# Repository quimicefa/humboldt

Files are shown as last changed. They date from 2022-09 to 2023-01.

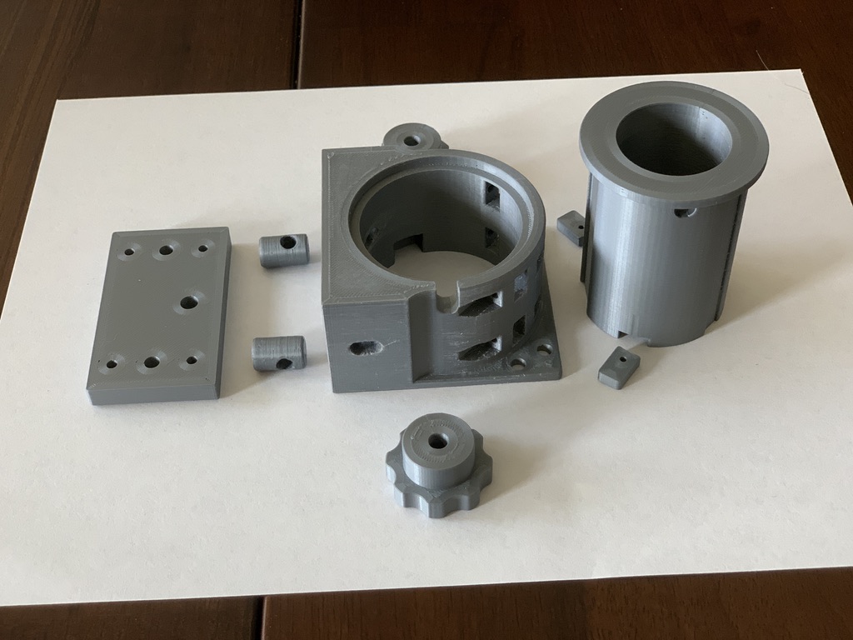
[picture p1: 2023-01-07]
focuser/images/focuser_125_ex_3D_PLA_parts.jpeg

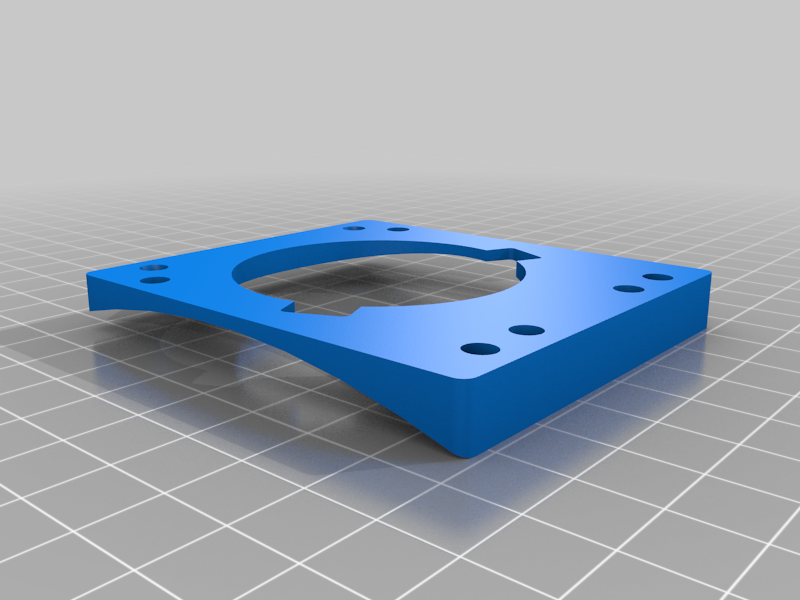
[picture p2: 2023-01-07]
focuser/images/focuser_1-25_curved_base_10-25_dia.png

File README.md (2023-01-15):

# Humboldt telescope
<p>Mashup from Leavitt LITE (Metric)</p>

<p>OTA by Aurelian on Printables: https://www.printables.com/es/model/355997-8-newtonian-telescope-leavitt-lite-metric</p>
<p>Crayford Focuser 1 1/4 inch by scbeme on Thingiverse: https://www.thingiverse.com/thing:5167331</p>

***

Focuser:

| id | Part | Dimensions | Material | Qty | Ref  | notes |
| -- | --- | --- | --- | ----- | ---- | --- |
| 1  | Drawtube | [Ref Drawing](focuser/files/focuser-drawtube_ver2.stl) | PLA | 1 | | |
| 2  | Base | [Ref Drawing](focuser/files/focuser_1-25_base.stl) | PLA | 1 | | |
| 3  | Curved base | [Ref Drawing](focuser/files/focuser_1-25_curved_base_10-25_dia.stl) | PLA | 1 | | Fits 10.25” OD tube |
| 4  | Pinion pressure rod | [Ref Drawing](focuser/files/focuser-pressure_cylinder_ver2.stl) | PLA | 2 | | |
| 5  | Base back | [Ref Drawing](focuser/files/focuser_1-25_back.stl) | PLA | 1 | | |
| 6  | Knob | [Ref Drawing](focuser/files/focuser-knob_ver2.stl) | PLA | 2 | | |
| 7  | Drawtube stop | [Ref Drawing](focuser/files/focuser_1-25_drawtube_stop_M2.stl) | PLA | 2 | | |
| 8  | Drawtube bearing rail | 2mm x 6mm x 60mm | Aluminium / Brass | 2 |  [LM-2](https://www.leroymerlin.es/productos/ferreteria-y-seguridad/perfiles-pletinas-chapas-y-rejillas/perfiles/plano-de-aluminio-gris-alt-0-2-x-an-1-5-x-l-100-cm-80109393.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) | |
| 9  | Drawtube pinion rail | 2mm x 12.5mm x 60mm | Aluminium | 1 |  [LM-2](https://www.leroymerlin.es/productos/ferreteria-y-seguridad/perfiles-pletinas-chapas-y-rejillas/perfiles/plano-de-aluminio-gris-alt-0-2-x-an-1-5-x-l-100-cm-80109393.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) | |
| 10 | M4 Philips head screw | 4mm x 20mm | Nylon | 1 | | Drawtube eyepiece capture screw |
| 11 | M3 button head hex drive screw | 3mm x 12mm | Stainless | 4+4 | | Base back / Curved base mounting screws |
| 12 | Pinion rod | d=4mm L=96mm | Stainless | 1 | [LM-1](https://www.leroymerlin.es/productos/ferreteria-y-seguridad/perfiles-pletinas-chapas-y-rejillas/perfiles/perfil-forma-redonda-de-acero-4mm-x-l-100-cm-80110632.html) | |
| 13 | Bearings | 8mm OD x 3mm ID x 4mm (693ZZ) | Stainless | 4 | [AE-2](https://www.aliexpress.com/item/4000980546028.html?spm=a2g0o.order_list.order_list_main.11.6c1218026v9wbl) | |
| 14 | M3 cap head hex screw | 3mm x 20mm | Stainless | 4 | | Bearing shafts |
| 15 | M3 flat washers | 3mm | Stainless | 8 | | Bearing shaft washers |
| 16 | M3 hex nuts | 3mm | Stainless | 4 | | Bearing shaft nuts |
| 17 | M3 heat set inserts | 3mm x 6mm L | Brass | 4+2+4 | [AE-1](https://www.aliexpress.com/item/1005003174906572.html?spm=a2g0o.order_list.order_list_main.5.21ef194dLnVGNK) | Base back / Knobs / Curved base |
| 18 | M4 heat set inserts | 4mm x 6mm L | Brass | 2 | [AE-1](https://www.aliexpress.com/item/1005003174906572.html?spm=a2g0o.order_list.order_list_main.5.21ef194dLnVGNK) | Eyepiece capture screw insert / Optional brake screw insert |
| 19 | M3 grub screws | 3mm x 6mm L | Stainless | 2+2+4 | | Knobs / Pinion pressure screws / Curved base alignment |
| 20 | M2 button head hex drive screw | 2mm x 8mm | Stainless | 2 | | Drawtube stops |
| 21 | M2 heat set inserts | 2mm x 6mm | Brass | 2 | [AE-1](https://www.aliexpress.com/item/1005003174906572.html?spm=a2g0o.order_list.order_list_main.5.21ef194dLnVGNK) | Drawtube stop inserts |

***
https://www.bauhaus.es/perfiles-metalicos-y-de-pvc/alberts-barra-plana/p/22847159
*** 

bearing rails (x2):
	w:6mm 
	l: 60mm
	t: 1mm
	
pinion rail (x1):
	w: 12.5mm
	l: 60mm
	t: 1.5mm

https://es.aliexpress.com/item/557757520.html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	
bearings (x4) 693ZZ:
	OD: 8mm
	ID: 3mm
	w: 4mm

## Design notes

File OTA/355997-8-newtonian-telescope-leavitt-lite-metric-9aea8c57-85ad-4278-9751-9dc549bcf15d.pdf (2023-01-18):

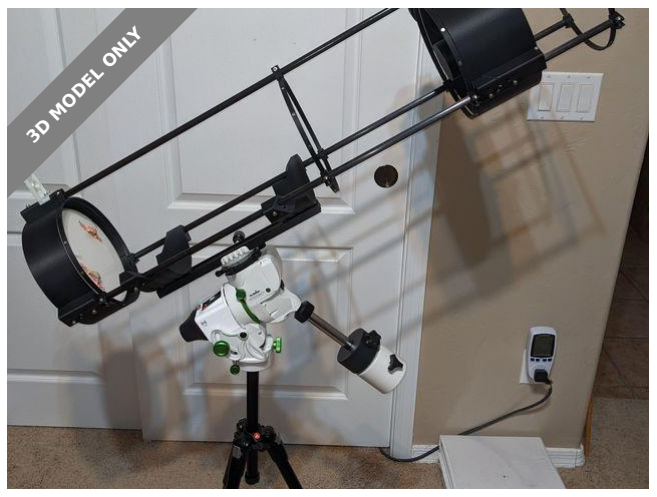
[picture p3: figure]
3D MODEL ONLY

## Summary

Based on Novel Tinker's 8" Leavitt keeping roughly the same design, but with the aim to be extremely lightweight (~8lbs)

Learning (https://printables.com/model?categoryId=90) > Physics & Astronomy (https://printables.com/model?categoryId=91)

Tags: astronomy | astrophotography | newtonian
newtoniantelescope | planets | reflector | science | stars

telescope

The Leavitt LITE takes the original Leavitt by Novel Tinker and does a few different notable things :

Use metric M4 screws & 12mm rods, this falls inline with a transition from the Hadley to Leavitt if you're coming from the official Hadley Metric Remix (https://www.printables.com/model/268580-hadley-telescope-remix-metric-mods-more)
Uses a 62.5mm secondary mirror (recommended (https://agenaastro.com/gso-parabolic-primary-telescope-mirror-8-f-5-ad049.html) for best uniform illumination on an F5 200mm mirror, can also cross reference with secondary mirror calculator (http://www.bbastrodesigns.com/NewtDesigner.html#diagonal)
Uses an overall smaller outer radius on parts (109mm) and thinner (but still sturdy) walls & rod interfaces to cut down on weight. It isn't much but it adds up!

Aurelian (https://printables.com/social/513907/about)

## 8" Newtonian Telescope "Leavitt"

## LITE (Metric)

VIEW IN BROWSER (https://printables.com/model/355997-8-newtonian-telescope-leavitt-lite-metric)

updated 17. 1. 2023 | published 17. 1. 2023

•

•

•

No conversion for Dobsonian mount, instead a mount interface for a Vixen Dovetail is provided with M5 screw holes
Slight modifications to spider + sights to fit new layout
Focuser clamp knob in case you don't want to buy thumb screws Primary cell changed to 120mm radius inner circle, 6 raised points of contact with small holes for better adhesion
Inner circle widening meant to both distribute the weight more and allow heatsinks to be attached to the back. My plan is to attach four 40mmx40mm heatsinks and have a quick-attach 120mm fan actively cool (WIP)

All that said, much of the credit and design goes to Novel Tinker for coming up with something that would fit on most print beds. Additionally, the basics of assembly instructions remains the same (using metric screws though) with some minor edits for QoL improvements:

Use two (2) triangular turn knobs for the secondary cell main height screw and on the primary cell adjustment screws (one on either side of the LTA so once collimated you can easily turn them to lock) for a total of eight (8) knobs (see close up photos)
You can use a spring as well on the primary cell adjustment screws, but the mirror is soooo heavy I wouldn't count on it Use a nut on underside of primary cell and on top of spider for secondary cell adjustments to lock screw (see close up photos)
Do the spider/secondary cell nut to lock the screw after collimation!
Can and probably should use a nut on the secondary cell main screw to lock in place
Put glue all along the top flat outer ring of the primary cell and then once mirror is placed along the rim on the underside, using finger or popsicle stick to smooth out. Last thing you want is your very expensive primary mirror falling out (see dead-on photo of back of primary mirror - all the silvery stuff is the glue)

Files that remain the same and should be sourced from the original Leavitt (https://www.printables.com/model/299531-8-newtonian-telescope-leavitt/files) :

Focuser grub
Focuser inner
Focuser ring
1.25 inch eyepiece adapter

##EDITS##

Added the blender file in which this was made. Unless you're computer is fast you may face some “issues” with it running slow, such is the nature of many many modifiers.

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
Added ribbed braced alternatives for the UTA, LTA could be done but is already fairly sturdy
Added a thicker spider alternative. Does cut down on light capture but is far sturdier
Added a little more tolerance to the secondary cell holder. Rising walls may be frail but that is okay, you should glue from the back anyways to avoid stressing the mirror during thermal acclimation

Overall using a mixture of the original Leavitt instructions and the above edits, the telescope is rock solid. In order to cut down on weight further I used 12mm 1000mm length carbon fiber rods. Pre-mirror installation the whole OTA including the ~300g long aluminum dovetail I have on it weighed 1660g (3.66lbs). With mirrors installed the OTA comes out to about 3855g (~8.5lbs)! This is light enough that I'm running it on a Star Adventurer GTI with accurate GoTo and tracking with a phone or camera attached (pictures of captures using these setups attached).

The whole purpose was to prove that you could do DSO astrophotography with maximal aperture (aperture is king alongside exposure - don't listen to those who say aperture isn't important) on a system that costs ~$1k USD. Likewise to prove that you can mount a large Newtonian on something less than an EQR-6. I will continue to post pictures taken with this setup, but a basic example of what can be done with standard stacking on a rather cheap mount is at the very end of pictures.

Secondary Mirror Graphs:

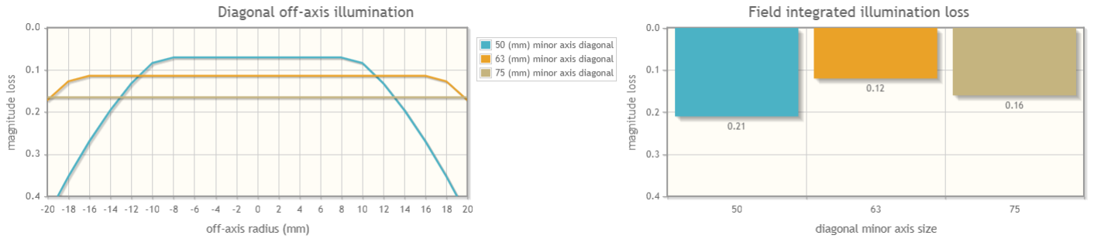
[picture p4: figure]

Notes:

Be careful tightening the secondary cell screws and screws pushing into the rods as you might flex the plastic and crack it (see last photos)

Be patient with the collimation process

If you want to do prime focusing you might want to pick up the alternate 1.25" eyepiece adapter to be able to push your focal point further down the focuser assembly (see Accessories down below)

Using nuts to compress-lock screws in place is a useful alternative to nylon locknuts and can work even better at times

•

•

•

For variable lengths on screws you can use the shorter length if you pad the hole with a little bit of cardboard. I did this since I don't like to have the screws press right up against the carbon fiber rods and scratch them up

My BOM for a very minimal setup using the QoL edits as seen in pictures i.e. two dovetail adapter pieces and not full ring, compression locking nuts, etc:

Screw Usage | Length mm (M4) | Quantity
Tube segment pushing on rods | 8-10 | 14
Mount sights and push on rods | 10-12 | 2
Mount sights, not on rods | 8-10 | 2
Join tube segments (slant) | 10 | 6
Spider to UTA, can push on rods | 16 | 3
Secondary cell main height | 50, 40 minimum* | 1
Secondary cell adjusters | 40, 32 minimum* | 3
Primary cell adjusters | 40, 32 minimum* | 3
Focuser clamp | 25 | 1
Focuser top panel mounting | 10 | 2
Focuser top panel grub lock | 16 | 2
Focuser front panel | 10 | 2
Focuser mounting to UTA | 10 | 4
Totals | Screw Size | Quantity
Assuming longer screws are used, use smaller screws as necessary if you buy an assortment set | M4x10mm | 30
| M4x12mm | 2
| M4x16mm | 2
| M4x25mm | 1
| M4x40mm | 6
| M4x50mm | 1
| M4 nuts | ~55+

Don't forget your mirrors (F5 / 200-203mm 1000mm focal length & 62.5 mm secondary) and 12mm rods!

8"
Newtonian
Telescope
"Leavitt"

## Model files

minimum* - You can get away with this shorter length but it will be difficult to have room to do adjustments

Accessories

Alternate 1.25" eyepiece adapter for being able to achieve prime focus and eyepiece focus as well (https://www.printables.com/model/356076-alternate-long-125-inch-eyepiece-adapter-for-leavi)

Secondary mirror minimal dust cover (https://www.printables.com/model/356075-625mm-secondary-mirror-dust-cover) (still working on primary mirror dust cover, but not high priority as I'm using the cheap plastic cover that came with the mirror)

## This remix is based on

8" Newtonian Telescope "Leavitt" (https://printables.com/model/299531-8-newtonian-telescope-leavitt) by Novel Tinker (https://printables.com/social/388837/about)

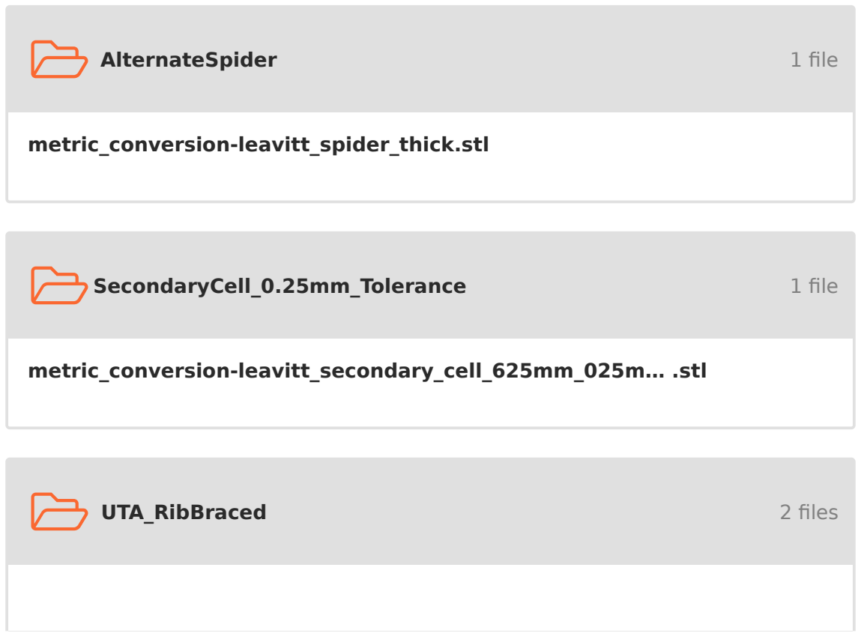
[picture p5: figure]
AlternateSpider; 1 file; SecondaryCell_0.25mm_Tolerance; UTA_RibBraced; 2 files; metric_conversion-leavitt_spider_thick.stl; metric_conversion-leavitt_secondary_cell_625mm_025m… .stl

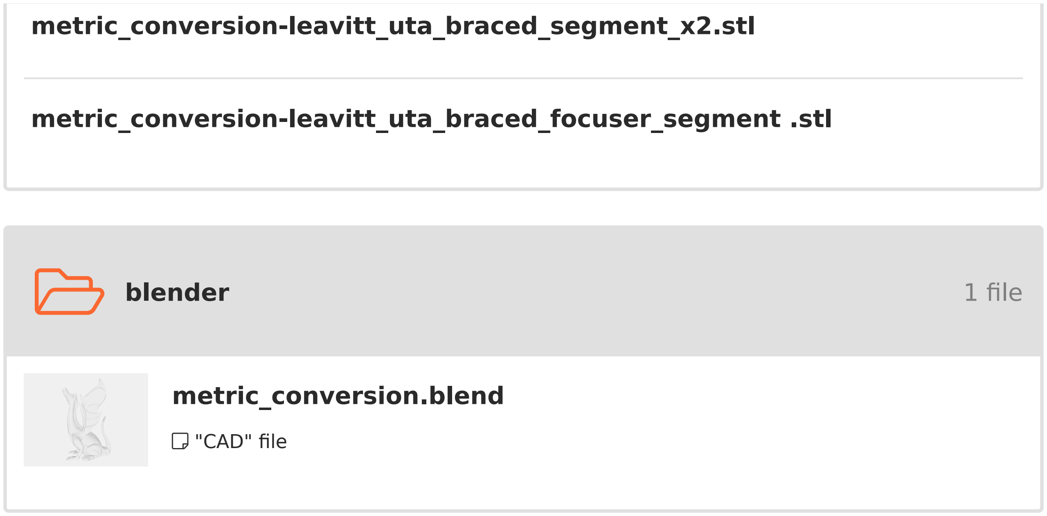
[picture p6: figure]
blender; 1 file; "CAD" file; metric_conversion-leavitt_uta_braced_segment_x2.stl; metric_conversion-leavitt_uta_braced_focuser_segment .stl; metric_conversion.blend

metric_conversion-leavitt_knob_x8.stl

metric_conversion-leavitt_eyepiece_clamp.stl

metric_conversion-leavitt_upper_sight.stl

metric_conversion-leavitt_focuser_grub_screw_panel.stl

metric_conversion-leavitt_lower_sight.stl

metric_conversion-leavitt_secondary_cell_625mm.stl

metric_conversion-leavitt_focuser_outer_top.stl

metric_conversion-leavitt_focuser_outer_bottom.stl

metric_conversion-leavitt_uta_segment_focuser.stl

metric_conversion-leavitt_dovetail_tubeattachsegmen… .stl

metric_conversion-leavitt_lta_segment_x3.stl

metric_conversion-leavitt_uta_segment_x2.stl

## License

This work is licensed under a
Creative Commons (4.0 International License)

Attribution-ShareAlike (http://creativecommons.org/licenses/by-sa/4.0/)

✖ | Sharing without ATTRIBUTION
✔ | Remix Culture allowed
✔ | Commercial Use
✔ | Free Cultural Works
✔ | Meets Open Definition

metric_conversion-leavitt_spider.stl

metric_conversion-leavitt_dovetail_tubeattachsegmen… .stl

metric_conversion-leavitt_primary_cell.stl

m4_knob.stl

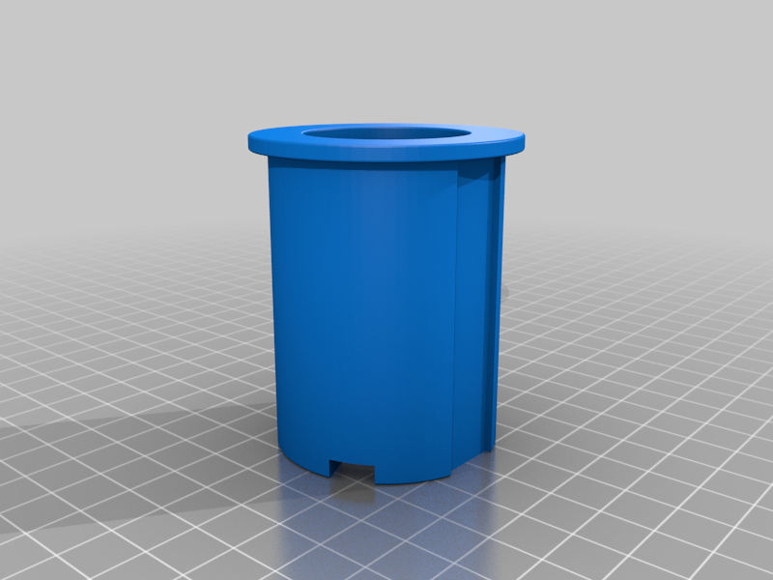
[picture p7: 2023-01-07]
focuser/images/focuser_1-25_drawtube.png

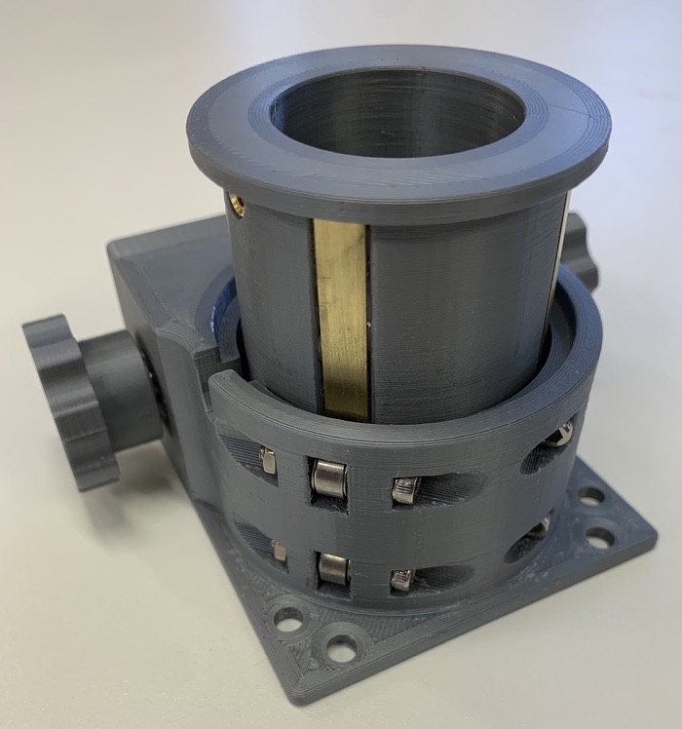
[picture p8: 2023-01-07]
focuser/images/focuser_125_ex_3D_frnt.jpeg

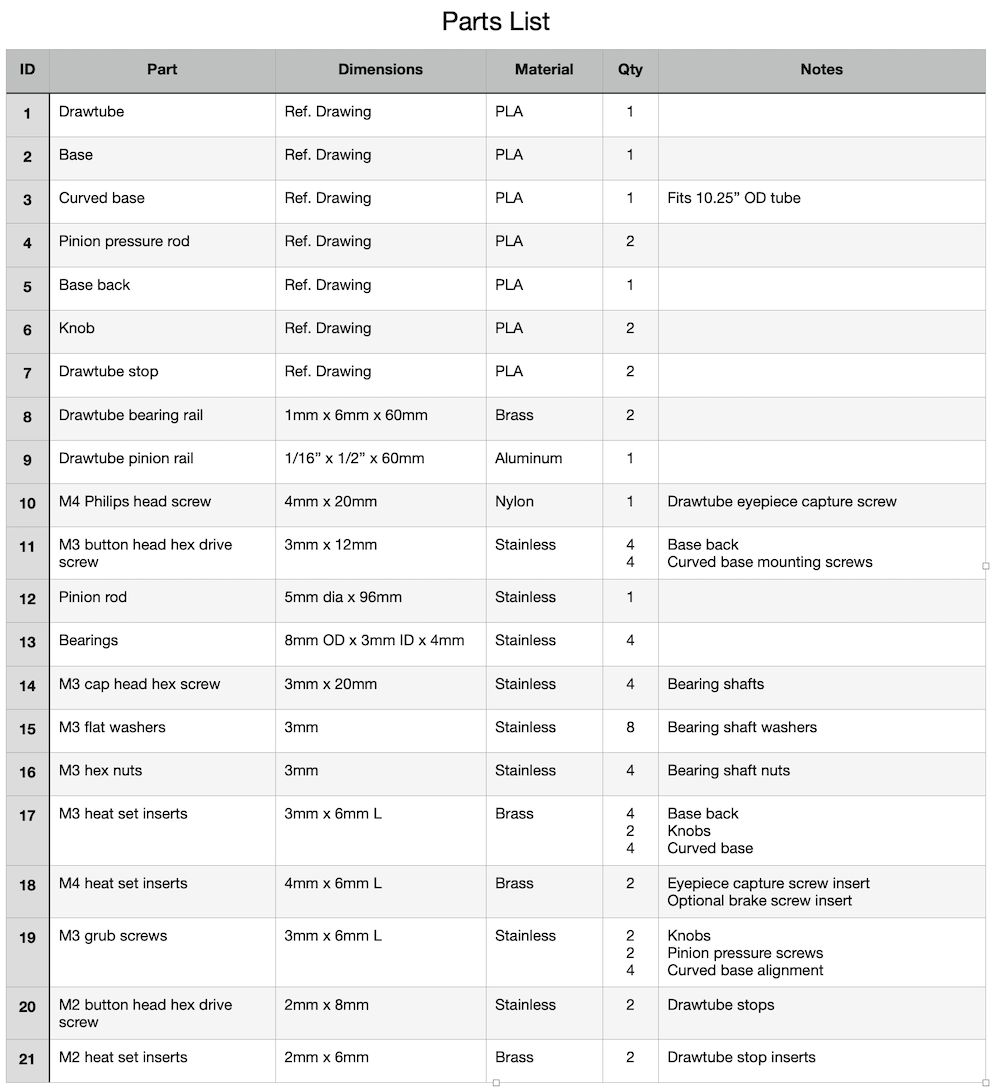
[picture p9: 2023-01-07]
focuser/images/focuser_125_PL_20211217.png

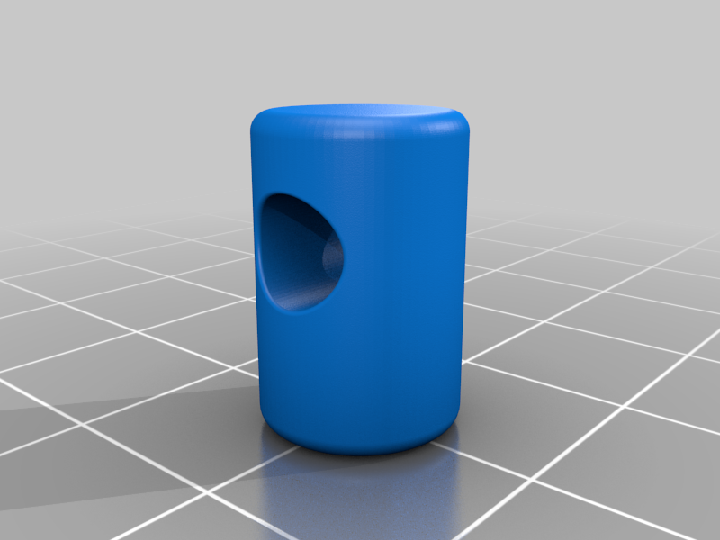
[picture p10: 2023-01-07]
focuser/images/focuser_1-25_pressure_cyl.png

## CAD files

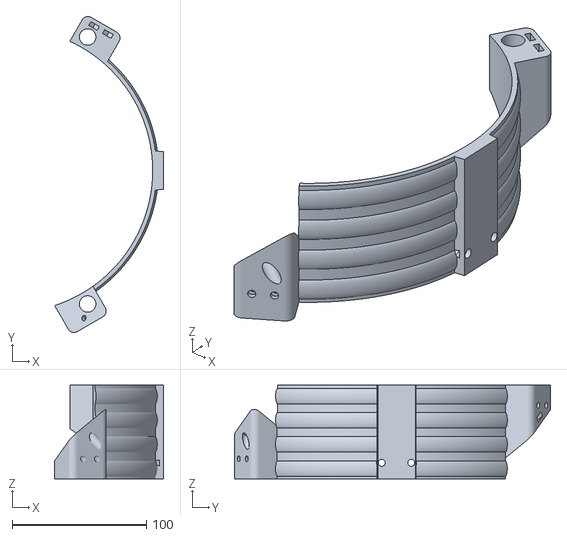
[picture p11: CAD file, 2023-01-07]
OTA/metric_conversion-Leavitt_Dovetail_TubeAttachSegment_Main.stl
81.1 x 235.8 x 70.0

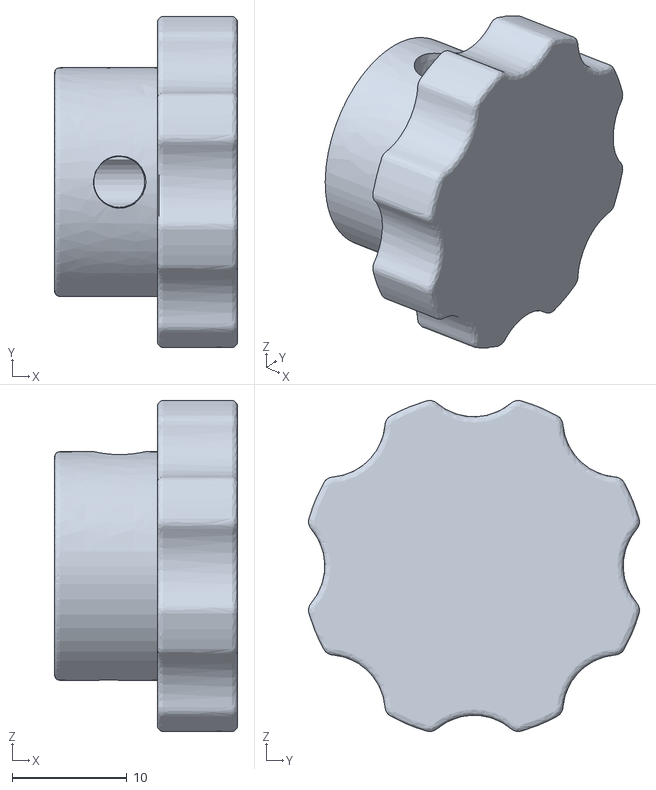
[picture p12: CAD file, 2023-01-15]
focuser/files/focuser-knob_ver2.stl
16.0 x 28.9 x 28.9

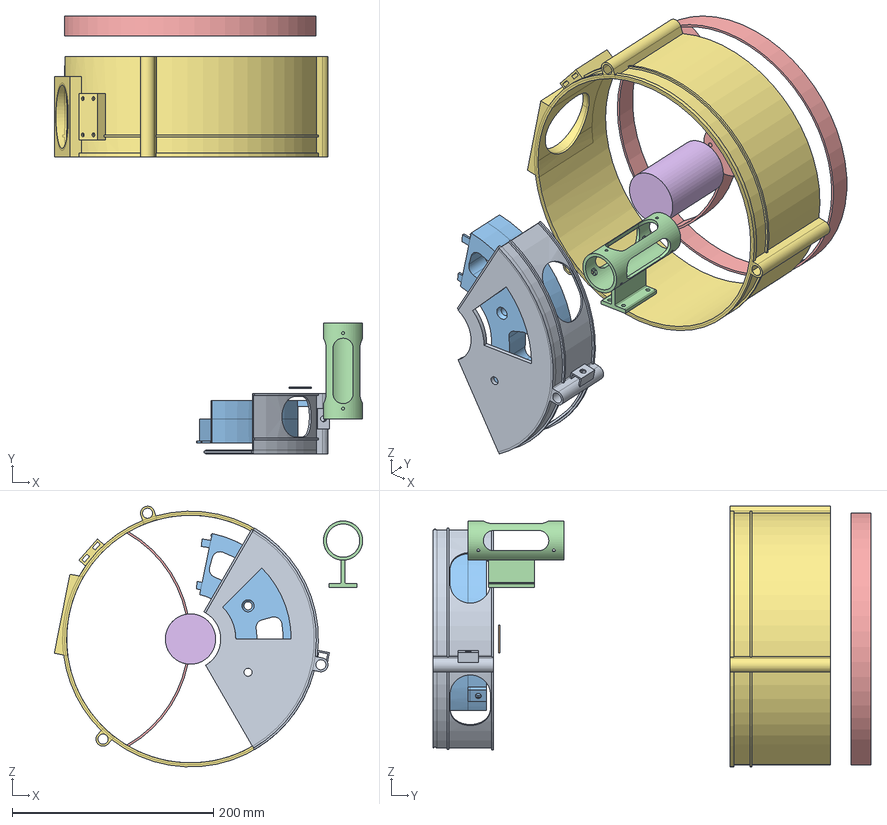
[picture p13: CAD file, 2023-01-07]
humboldt-2.FCStd
306.3 x 435.0 x 258.8 mm
backplate
primary.tab
primary.cell
finderscope
spider001
secondary

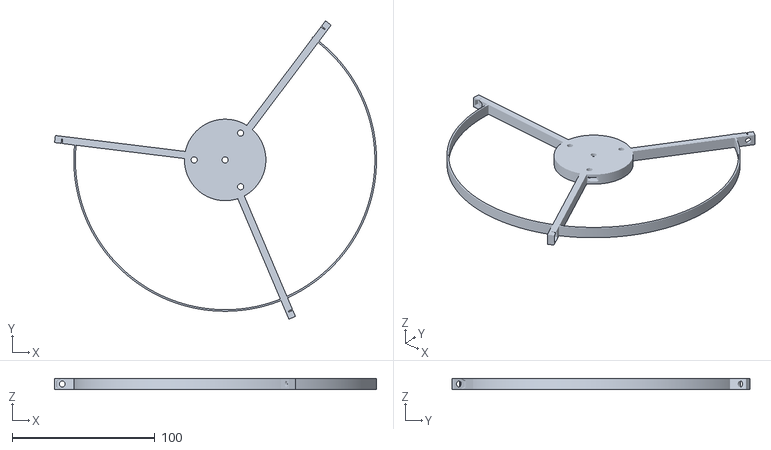
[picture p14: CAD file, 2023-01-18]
OTA/AlternateSpider/metric_conversion-Leavitt_Spider_Thick.stl
225.3 x 208.8 x 8.00

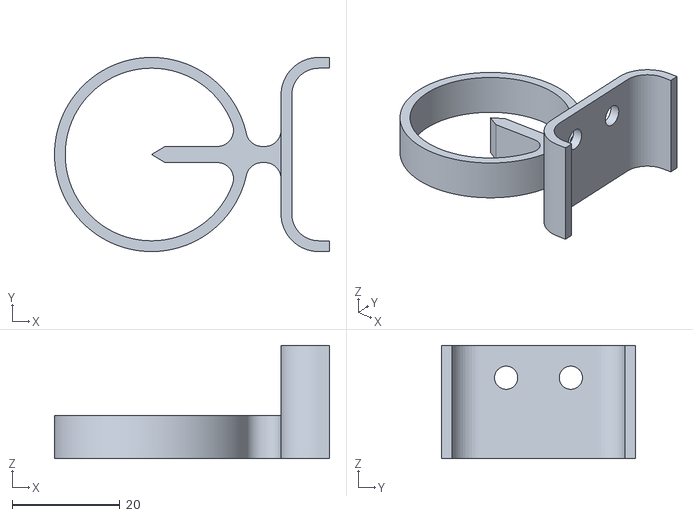
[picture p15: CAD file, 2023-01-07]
OTA/metric_conversion-Leavitt_Upper_sight.stl
51.0 x 36.0 x 21.0

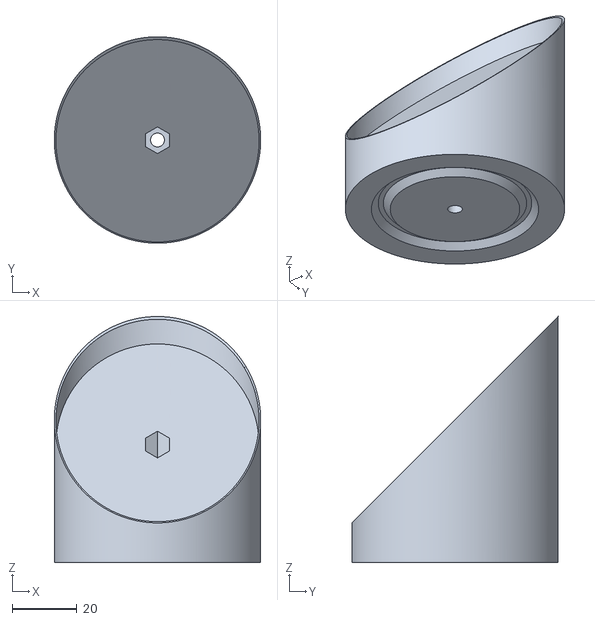
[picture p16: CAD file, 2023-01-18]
OTA/SecondaryCell_0.25mm_Tolerance/metric_conversion-Leavitt_Secondary_cell_62.5mm_0.25mm_tol.stl
64.0 x 64.0 x 76.3

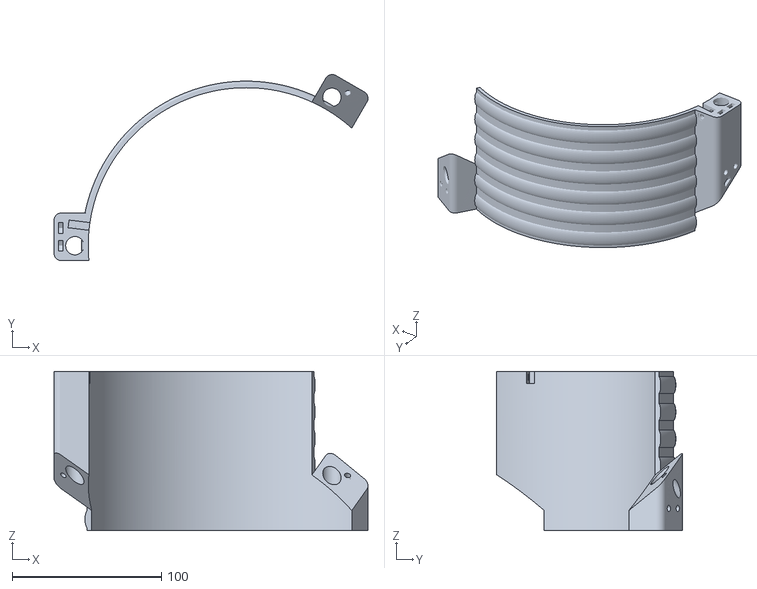
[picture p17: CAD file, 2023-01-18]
OTA/UTA_RibBraced/metric_conversion-Leavitt_UTA_Braced_Segment_x2.stl
210.7 x 124.8 x 107.0

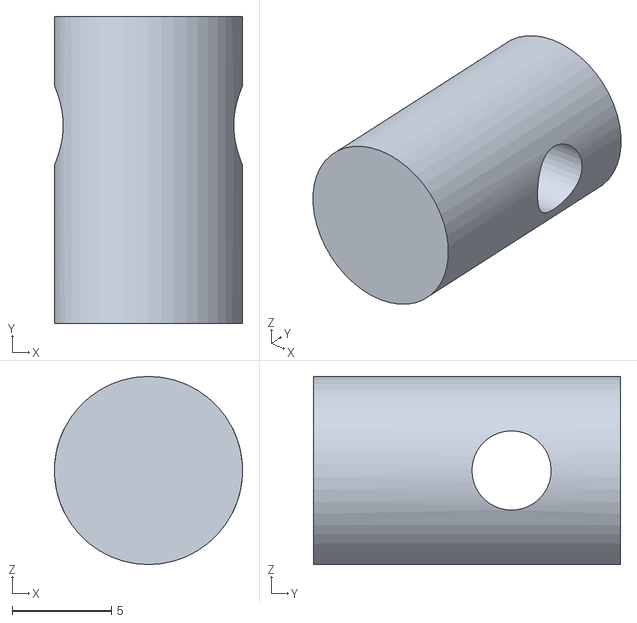
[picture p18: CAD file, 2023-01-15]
focuser/files/focuser-pressure_cylinder_ver2.stl
9.50 x 15.5 x 9.50

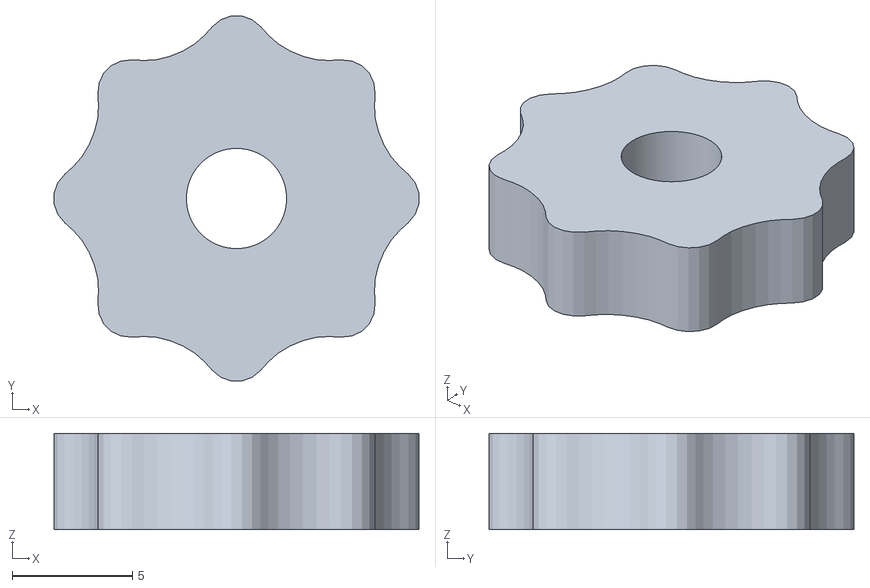
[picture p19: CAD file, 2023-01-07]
OTA/m4_knob.stl
15.2 x 15.2 x 4.00

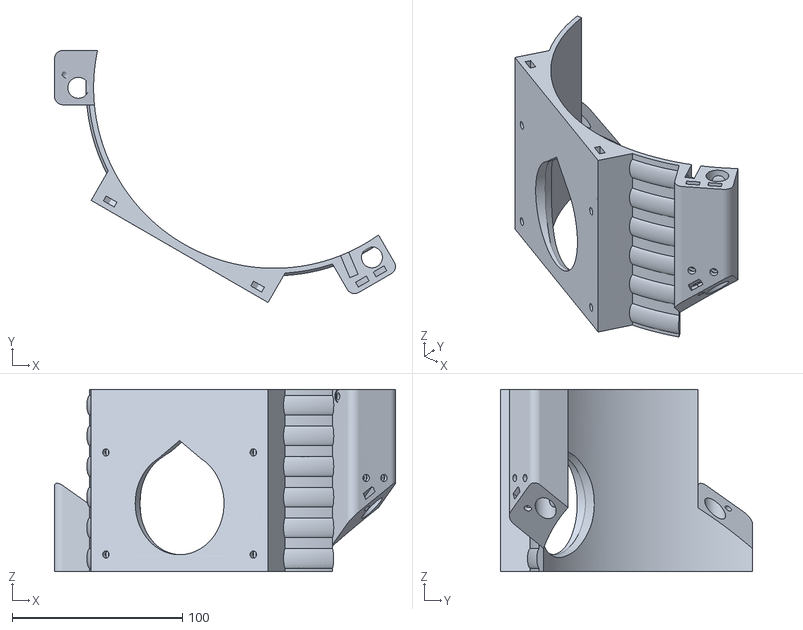
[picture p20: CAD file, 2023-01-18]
OTA/UTA_RibBraced/metric_conversion-Leavitt_UTA_Braced_Focuser_Segment.stl
200.3 x 148.1 x 107.0

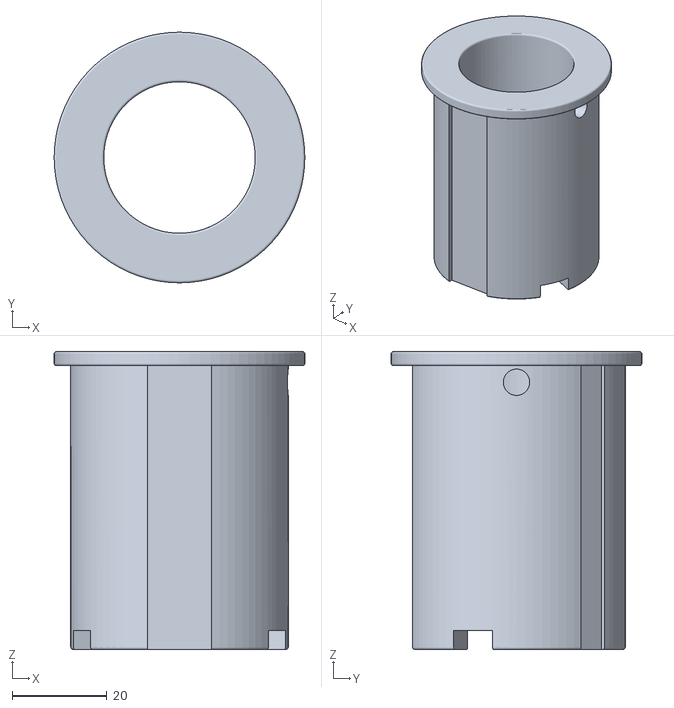
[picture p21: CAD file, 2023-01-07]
focuser/files/focuser_1-25_drawtube.stl
53.0 x 53.0 x 63.0

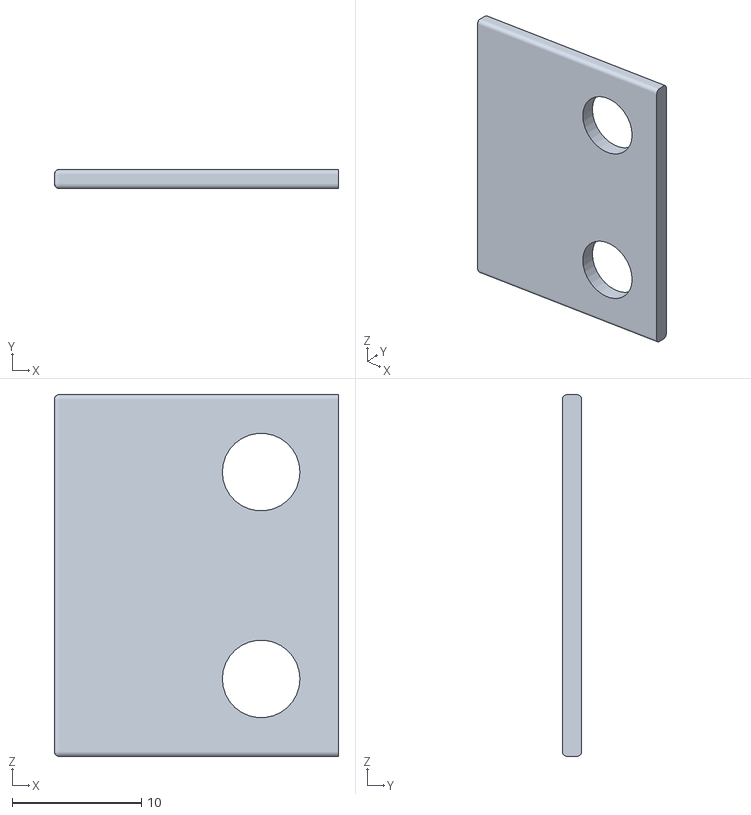
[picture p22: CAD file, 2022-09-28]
humboldt-1-primary.tab.stl
22.0 x 1.50 x 28.0

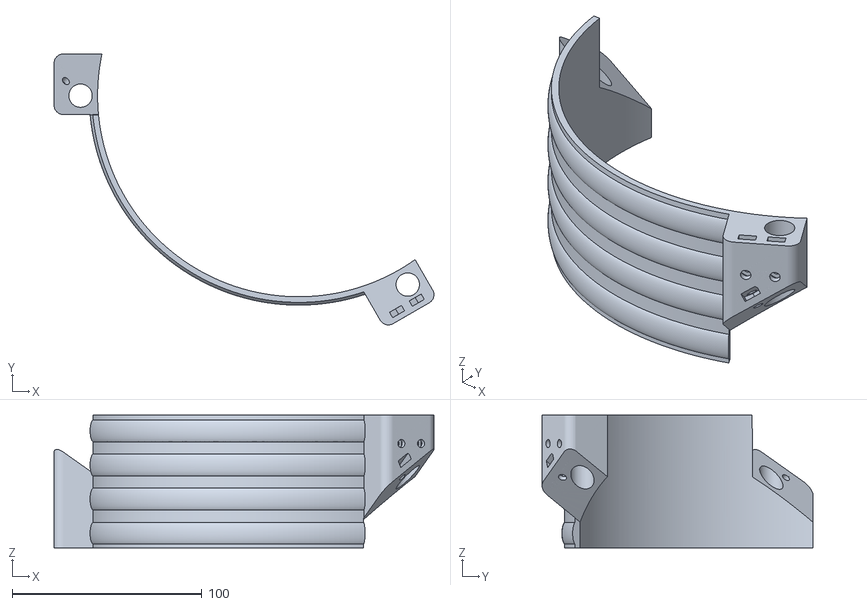
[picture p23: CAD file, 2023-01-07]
OTA/metric_conversion-Leavitt_Dovetail_TubeAttachSegment_x2.stl
200.3 x 142.8 x 70.0

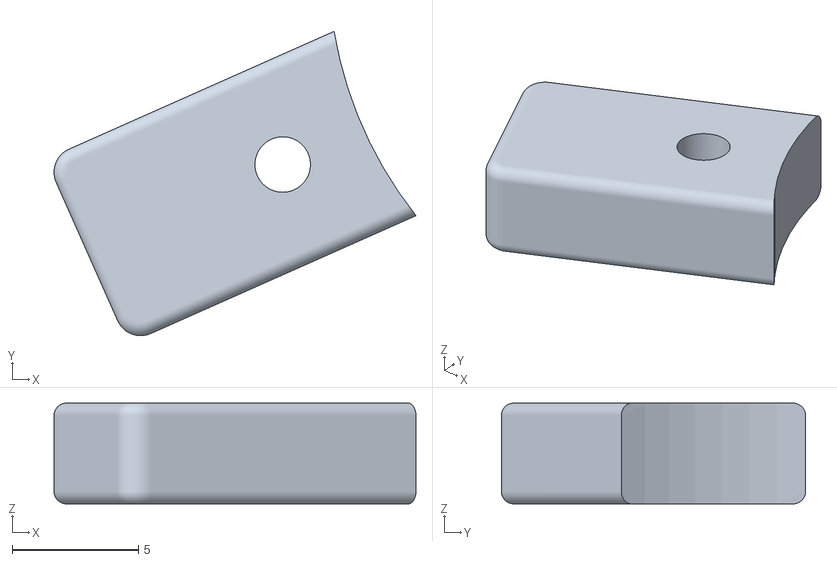
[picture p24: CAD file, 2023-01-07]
focuser/files/focuser_1-25_drawtube_stop_M2.stl
14.4 x 12.1 x 4.00

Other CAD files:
focuser/focuser.FCStd
humboldt-1.FCStd
OTA/metric_conversion-Leavitt_Secondary_cell_62.5mm.stl
focuser/files/focuser_1-25_knob.stl
OTA/blender/metric_conversion.blend
OTA/metric_conversion-Leavitt_Eyepiece_clamp.stl
OTA/metric_conversion-Leavitt_Focuser_grub_screw_panel.stl
OTA/metric_conversion-Leavitt_Focuser_outer_bottom.stl
OTA/metric_conversion-Leavitt_Focuser_outer_top.stl
OTA/metric_conversion-Leavitt_Knob_x8.stl
OTA/metric_conversion-Leavitt_LTA_Segment_x3.stl
OTA/metric_conversion-Leavitt_Lower_sight.stl
OTA/metric_conversion-Leavitt_Spider.stl
OTA/metric_conversion-Leavitt_UTA_Segment_Focuser.stl
OTA/metric_conversion-Leavitt_UTA_Segment_x2.stl
focuser/files/focuser_1-25_back.stl
focuser/files/focuser_1-25_base.stl
focuser/files/focuser_1-25_curved_base_10-25_dia.stl
focuser/files/focuser_1-25_pressure_cyl.stl

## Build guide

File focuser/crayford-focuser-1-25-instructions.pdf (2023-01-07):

LeisureNotes.com

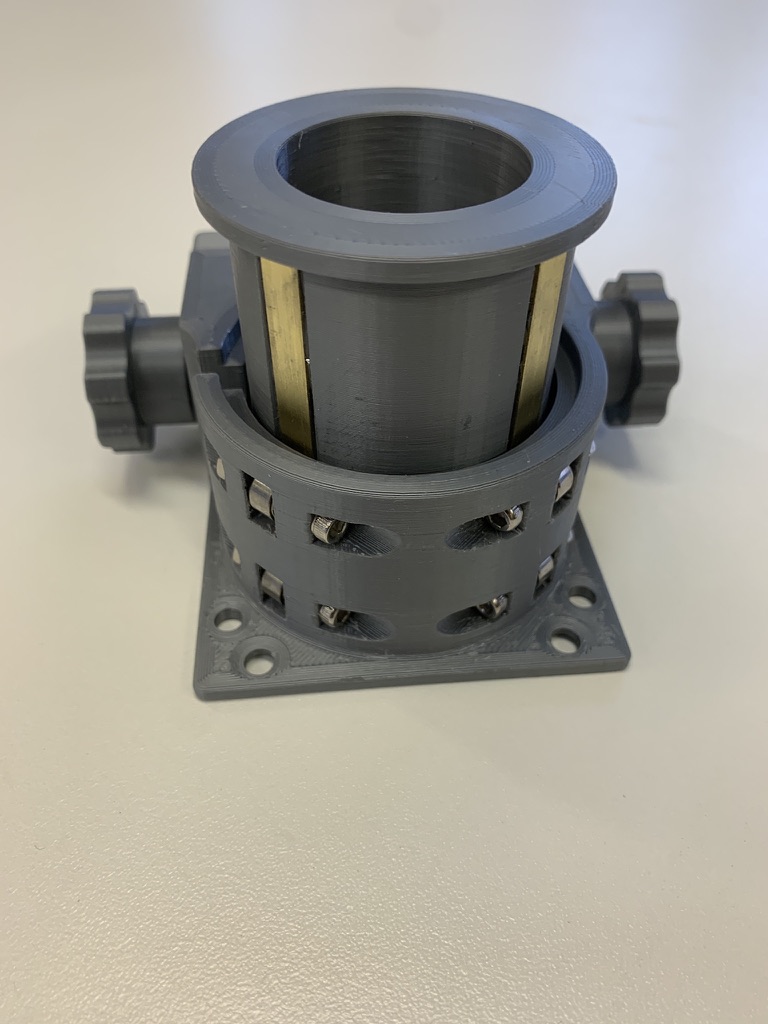
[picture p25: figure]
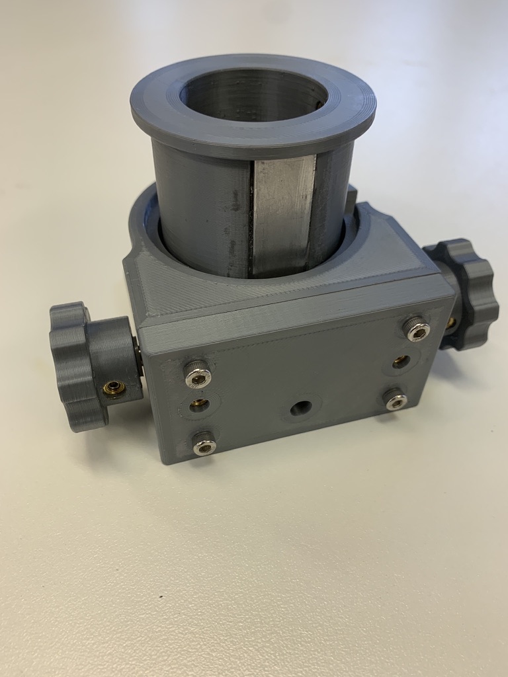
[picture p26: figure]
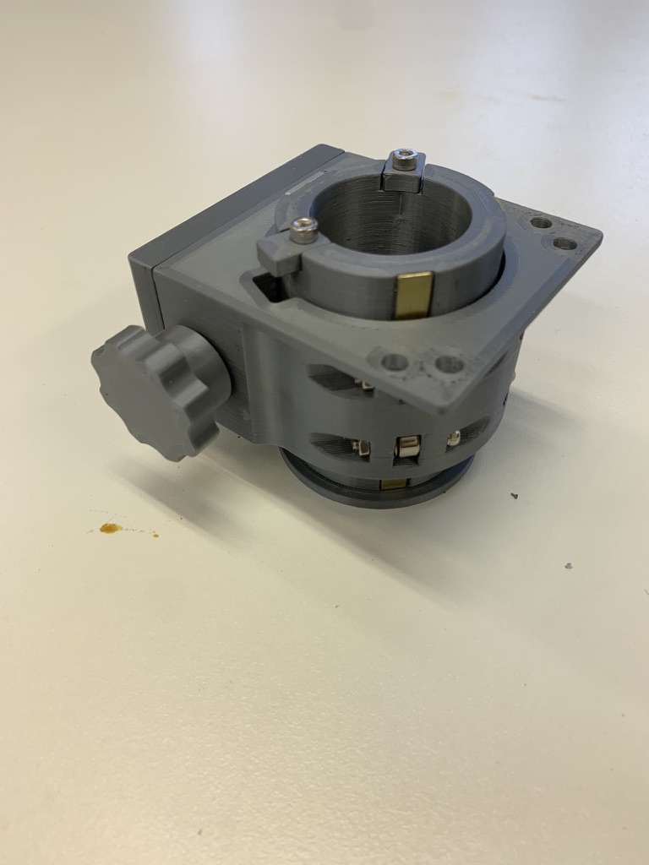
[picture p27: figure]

# 1 1/4” Crayford Focuser

# 3D Printed Focuser

I wanted to use a 1 1/4” focuser for an 8” Newtonian telescope I was making. But most commercial crayford focusers are designed for 2” eyepieces which are a bit large for an 8” telescope. So I decided to make use of my 3D printer and create my own 1 1/4” crayford focuser. My design fits a 10” diameter tube, but one could easily modify the design if a flat base is needed.

My focuser works just like any other crayford focuser. Turn the knob and the drawtube smoothly, with no backlash, moves up or down until a stop is reached. The drawtube friction is adjusted using the two tensioning grub screws on the focuser back. Also on the back is an optional M4 threaded hole to add a brake if using heavier accessories. My heaviest eyepiece is a 24mm Televue Panoptic eyepiece which works fine without the brake.

Here are a few of the key focuser design attributes (with a 2mm thick curved base added):
- Drawtube inside diameter = 1 1/4”
- Minimum racked-in height = 40mm
- Maximum racked-out height = 70mm
- Drawtube travel = 30mm
- Maximum drawtube extension below base = 23mm
- Weight = 200g
- 3D print material = PLA
- Curved base mounting holes: 48mm x 63mm
- Base dimensions: 68mm x 77mm

Want to build your own focuser? You can either download my STL files and start printing. Or download my 3D model CAD files and create your own customized version.

These instructions include the following:

1. 1 1/4” crayford focuser example (See above photo).
2. Construction Tips
3. Parts List + Exploded View
4. Downloadable Files (LeisureNotes.com)
1. Instructions (pdf file)
2. 3D CAD Models
1. STEP (zip)
2. STP (zip)
3. OBJ (zip)
4. STL (zip; also available at Thingiverse)
Please note that this 3D printed focuser design has also been shared on the Thingiverse website. Simply click this Thingiverse link or search for Thingiverse project # ?????.

## Construction Tips

First, my disclaimer. I rate myself as a novice 3D printer user. So please don’t hesitate to modify my design to better suit your 3D printing capabilities.

Here are the 3D printer settings I used:
- Printer: Prusa MK3S+
- Slicer app: PrusaSlicer
- Filament: Prusament PLA
- Nozzle temperature: 215
- Bed temperature: 60
- Layer height: 0.20mm
- Supports:
- Drawtube — none
- Printed with top end on platter
- Base — everywhere
- Note: Rookie mistake here. I had support material everywhere. In hindsight, I suspect the base can be printed with very little support material. The most likely spots are the two pinion rod pressure rods.
- Printed with focuser base on printer platter
- Perimeters: 6
- Solid layers (top and bottom): 8
- Minimum shell thickness (top and bottom): 0.7mm

So you now have the settings that worked for me. Again, I’m a novice using my 3D printer and I suspect some of my perimeter and layer settings might be overkill.

Also please make sure you compare your printer tolerances with my mine. The inside hole diameters printed using my printer average 0.2mm smaller than the CAD diameter setting. So my 3D models have holes that are intentionally 0.2mm diameter larger so the final, printed hole sizes will be very close to the required size. For example, if I need a 3mm hole diameter for a M3 screw, my 3D model will have a 3.2mm diameter hole.

## Build Steps

Drawtube
1. 3D print the drawtube.
2. Lightly sand the three drawtube rail recesses used for the pinion aluminum rail and two brass bearing rails.
3. Cut the metal rails to length, check the fit, clean and rough up both sides with sandpaper, and then glue the metal rails to the drawtube. I used the JB Weld original epoxy which I highly recommend. Make sure you clamp the rails to the drawtube for a strong glue joint. For clamps, I place a small piece of scrap wood on top of each metal rail and then used rubber bands as ‘clamps’ to press the metal strips against the drawtube.
4. Install the heat set brass inserts for the eyepiece retainer screw and the two drawtube stops in the bottom end. Note that my example focuser has M3 screws for the stops, but I recommend M2 screws. The design (and CAD files) have been revised to use the recommended M2 screws.

Focuser Base
1. 3D print the base. Remember, I used ‘everything’ setting for my support material. I don’t recommend this setting since every hole in my focuser base had support material which was difficult to remove. If I build another one, I’ll use the PrusaSlicer tool to selectively add support material to the few necessary areas such as the two holes for the pinion pressure rods.
2. Install into the base the four heat set inserts for the base back plate and the one insert for the optional brake. Next I installed the two pressure grub screws into the base back plate. Note that I installed the two grub screw inserts from the backside of the back plate which increases the holding strength. I also went ahead and installed the heat inserts into the two knobs.
3. Install the four drawtube pressure bearings that fit against the drawtube brass rails. Don’t forget the flat washers which act as spacers between the bearings and the base.
4. Next I did a quick fit check for the pinion shaft which should turn freely. My holes were a little small so I carefully used a drill bit to slightly enlarge the holes. Making these holes slightly larger might be a nice design improvement if I every do another revision.
5. Time to install the pinion pressure rods. First, I cleaned out the holes in the base where the pressure rods are inserted. These two holes needed some minor cleaning/rounding (especially the seam along the top). Then I did a trial fit of the pressure rods which needed a light sanding for a snug fit. I wanted these rods to fit with no ‘slop’ since once the pressure is set no further rod movement is needed.
6. Next, I inserted the pinion rod and checked the fit to ensure I had a close tolerance fit and smooth turning. Then I did a push-pull of the pinion rod to check that the pressure rods would also move in-out correctly.
7. Now that main moving parts seemed to be working, I installed the base back using four M3 screws. Then I added the two grub screws used to push the pinion rod against the drawtube.
8. Before tightening the pressure grub screws, I added the drawtube.
9. Next I installed the two knobs.
10. Now I carefully tightened the pressure grub screws (needed very little pressure) until the drawtube had enough pressure to operate smoothly plus held my eyepiece in position.
11. Finally, I added the two drawtube stops and the drawtube M4 nylon screw used to capture the eyepiece in the drawtube.

All done! …almost…

Please note that my focuser mounts to a 10.25” OD telescope tube. So I printed and glued a curved base to the bottom of my focuser (adds 2mm to the focuser base height). I then added the heat set inserts for the four mounting screws which are inserted from inside the telescope tube (bottom of focuser). Next I added the inserts for the four alignment grub screws which are installed and accessed from the focuser side of the telescope tube.

## Parts

The parts I used are all easily located online. I purchased most of my parts from Amazon. I also highly recommend McMaster-Carr as an excellent online supplier. You can use the following exploded views along with the parts list to help you visualize the focuser design. Of course using a 3D model file viewer or CAD program is highly recommended.

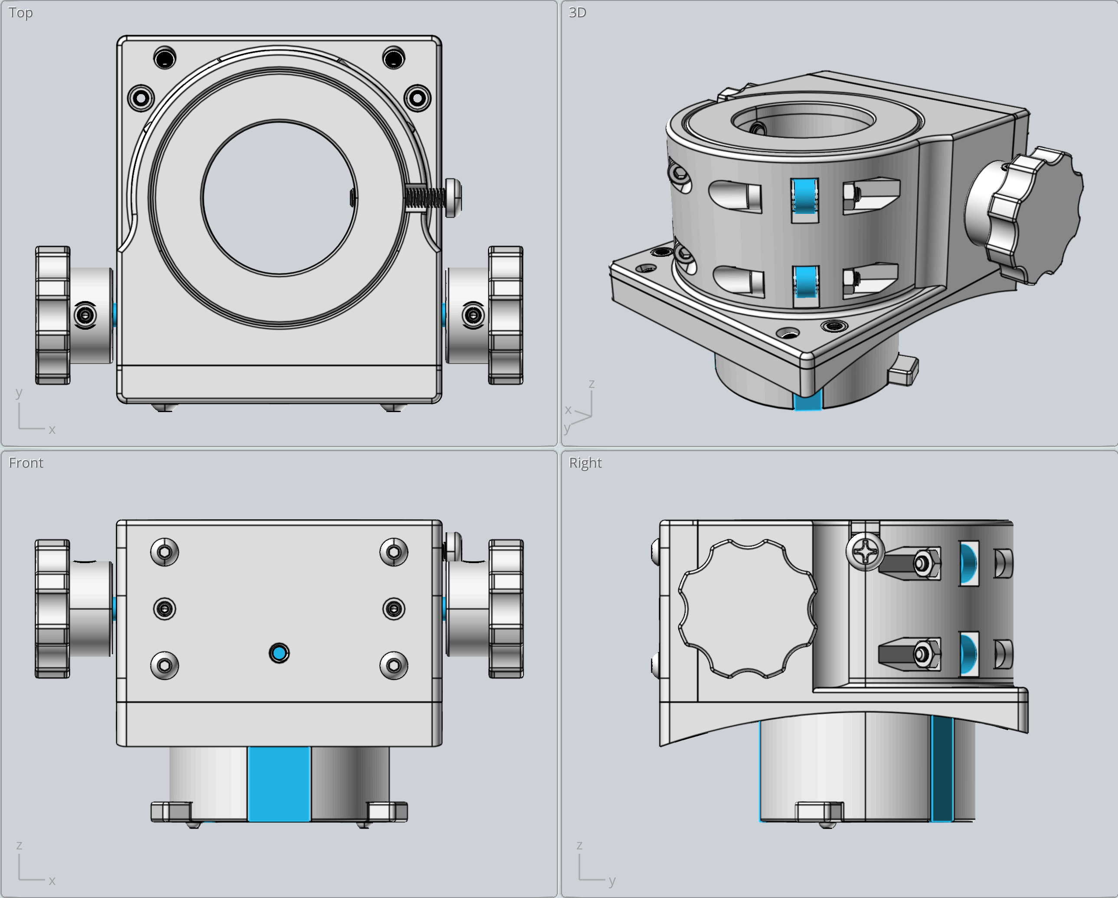
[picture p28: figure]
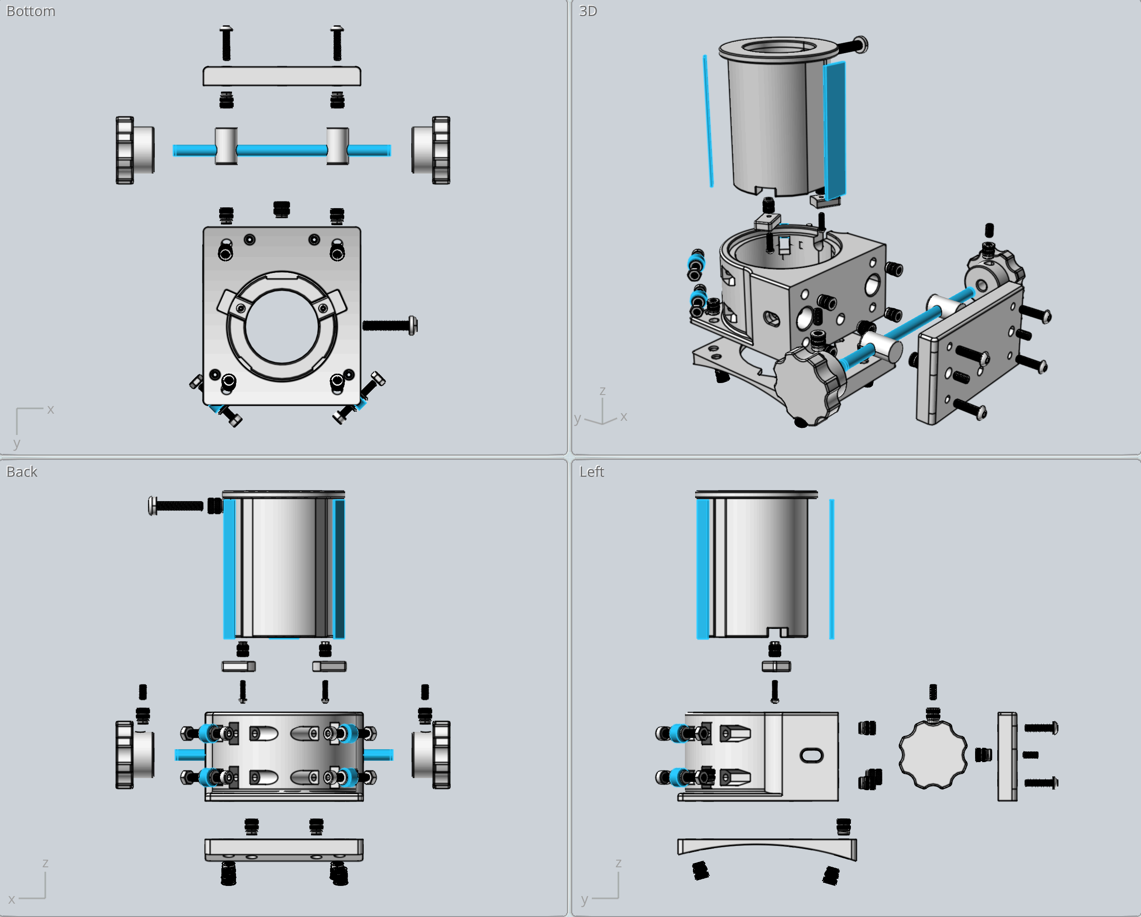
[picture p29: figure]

Parts List

ID | Part | Dimensions | Material | Qty | Notes
1 | Drawtube | Ref. Drawing | PLA | 1
2 | Base | Ref. Drawing | PLA | 1
3 | Curved base | Ref. Drawing | PLA | 1 | Fits 10.25” OD tube
4 | Pinion pressure rod | Ref. Drawing | PLA | 2
5 | Base back | Ref. Drawing | PLA | 1
6 | Knob | Ref. Drawing | PLA | 2
7 | Drawtube stop | Ref. Drawing | PLA | 2
8 | Drawtube bearing rail | 1mm x 6mm x 60mm | Brass | 2
9 | Drawtube pinion rail | 1/16” x 1/2” x 60mm | Aluminum | 1
10 | M4 Philips head screw | 4mm x 20mm | Nylon | 1 | Drawtube eyepiece capture screw
11 M3 button head hex drive | screw | 3mm x 12mm | Stainless | 4 4 | Base back Curved base mounting screws
12 | Pinion rod | 5mm dia x 96mm | Stainless | 1
13 | Bearings | 8mm OD x 3mm ID x 4mm | Stainless | 4
14 | M3 cap head hex screw | 3mm x 20mm | Stainless | 4 | Bearing shafts
15 | M3 flat washers | 3mm | Stainless | 8 | Bearing shaft washers
16 | M3 hex nuts | 3mm | Stainless | 4 | Bearing shaft nuts
17 | M3 heat set inserts | 3mm x 6mm L | Brass | 4 2 4 | Base back Knobs Curved base
18 | M4 heat set inserts | 4mm x 6mm L | Brass | 2 | Eyepiece capture screw insert Optional brake screw insert
19 | M3 grub screws | 3mm x 6mm L | Stainless | 2 2 4 | Knobs Pinion pressure screws Curved base alignment
20 M2 button head hex drive | screw | 2mm x 8mm | Stainless | 2 | Drawtube stops
21 | M2 heat set inserts | 2mm x 6mm | Brass | 2 | Drawtube stop inserts

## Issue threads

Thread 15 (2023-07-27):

secondary holder + cap

quimicefa, 2023-07-27:
-shorter ribbon in sec holder.
-stopper in sec holder.
-check screw dimensions . should fit a M5 hex cap.

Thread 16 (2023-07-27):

fix finderscope holder dimensions

quimicefa, 2023-07-27:
-findescope dimensions
-finderscope screws -> M3

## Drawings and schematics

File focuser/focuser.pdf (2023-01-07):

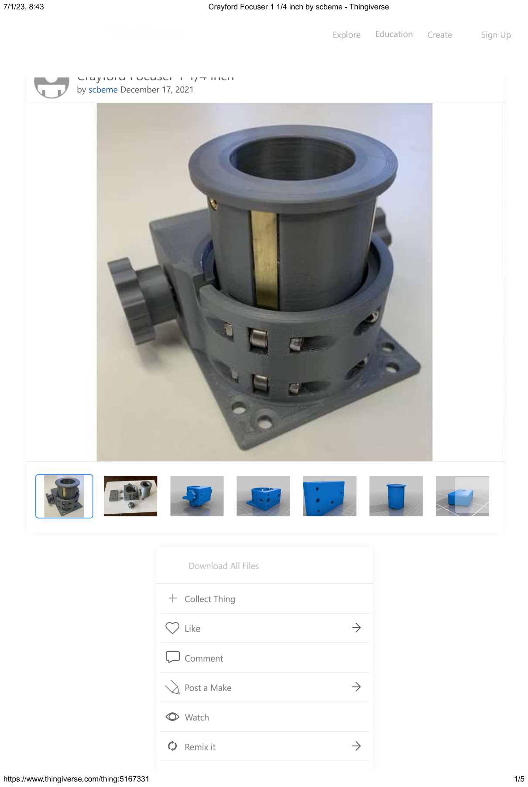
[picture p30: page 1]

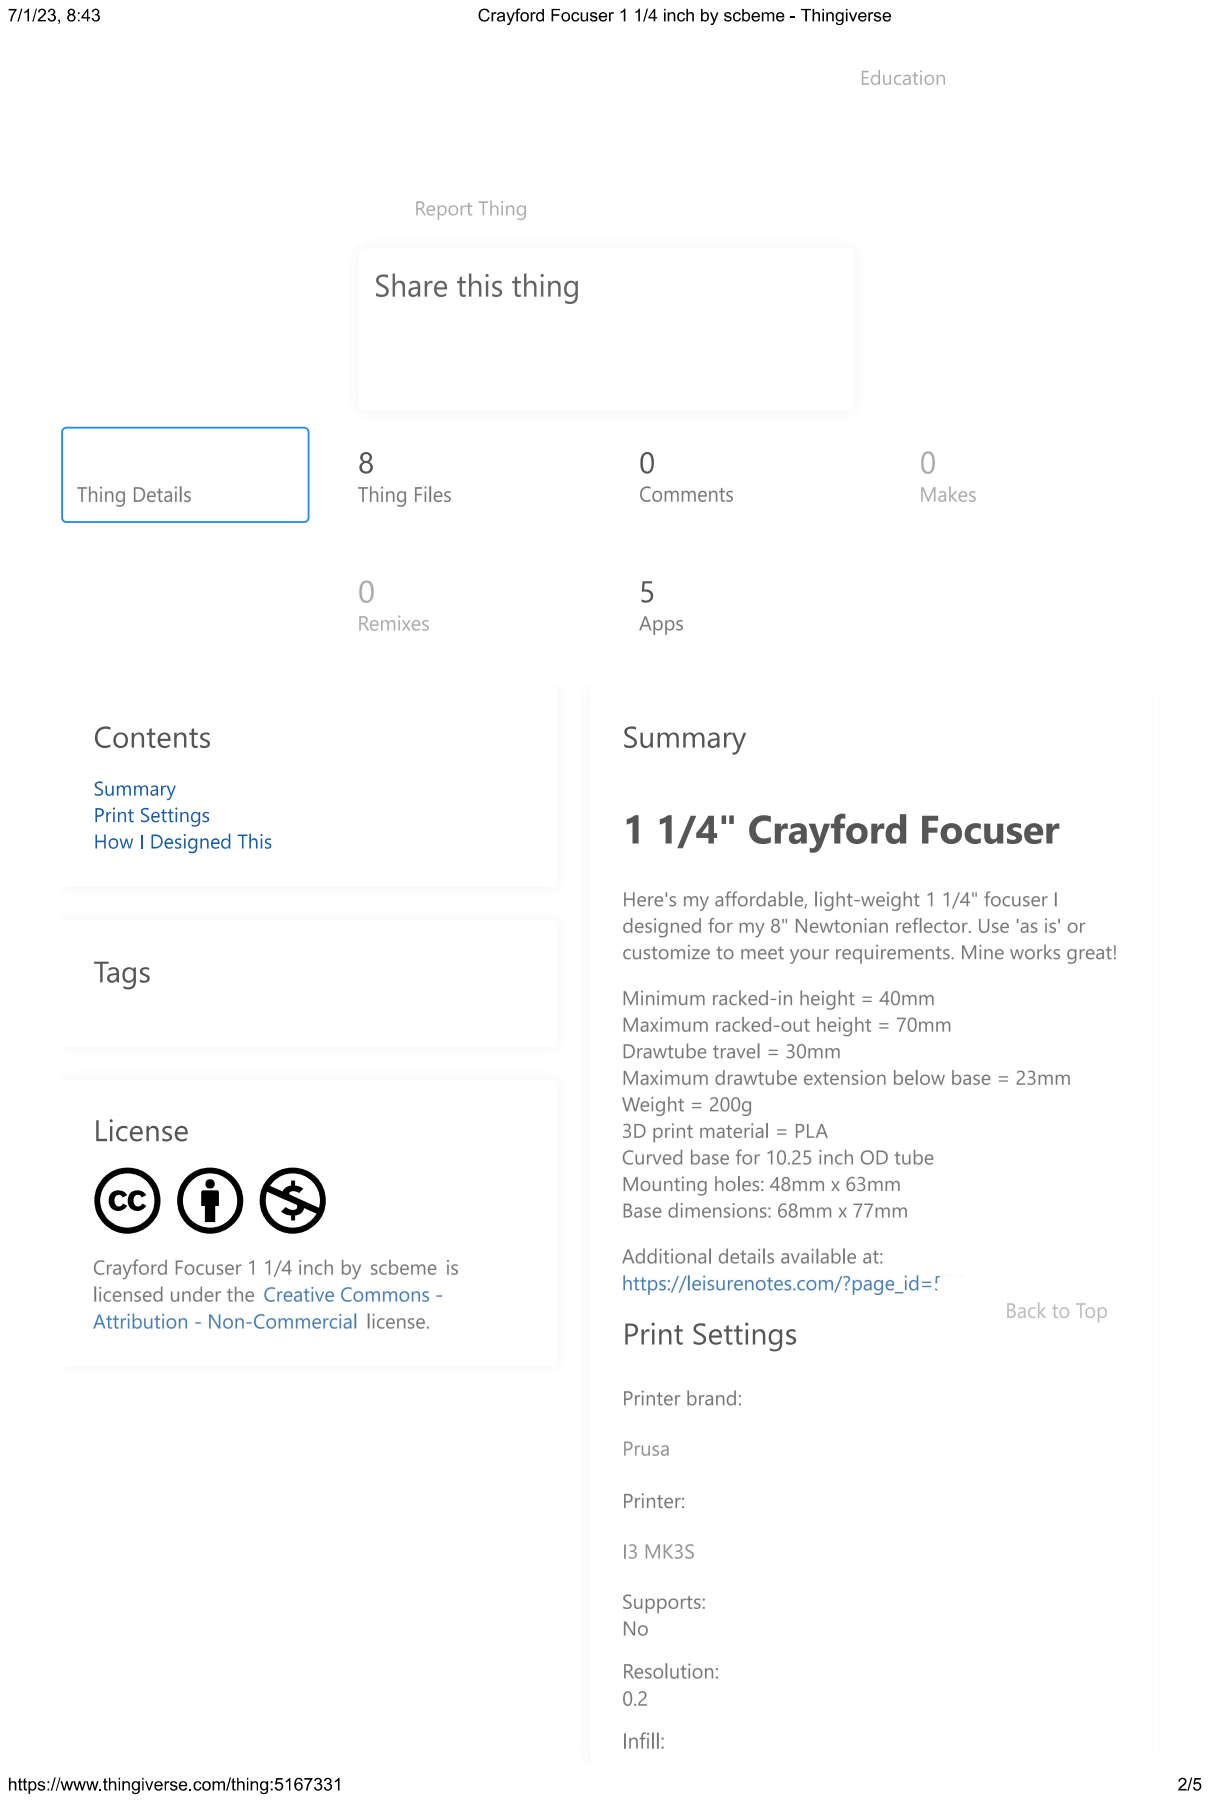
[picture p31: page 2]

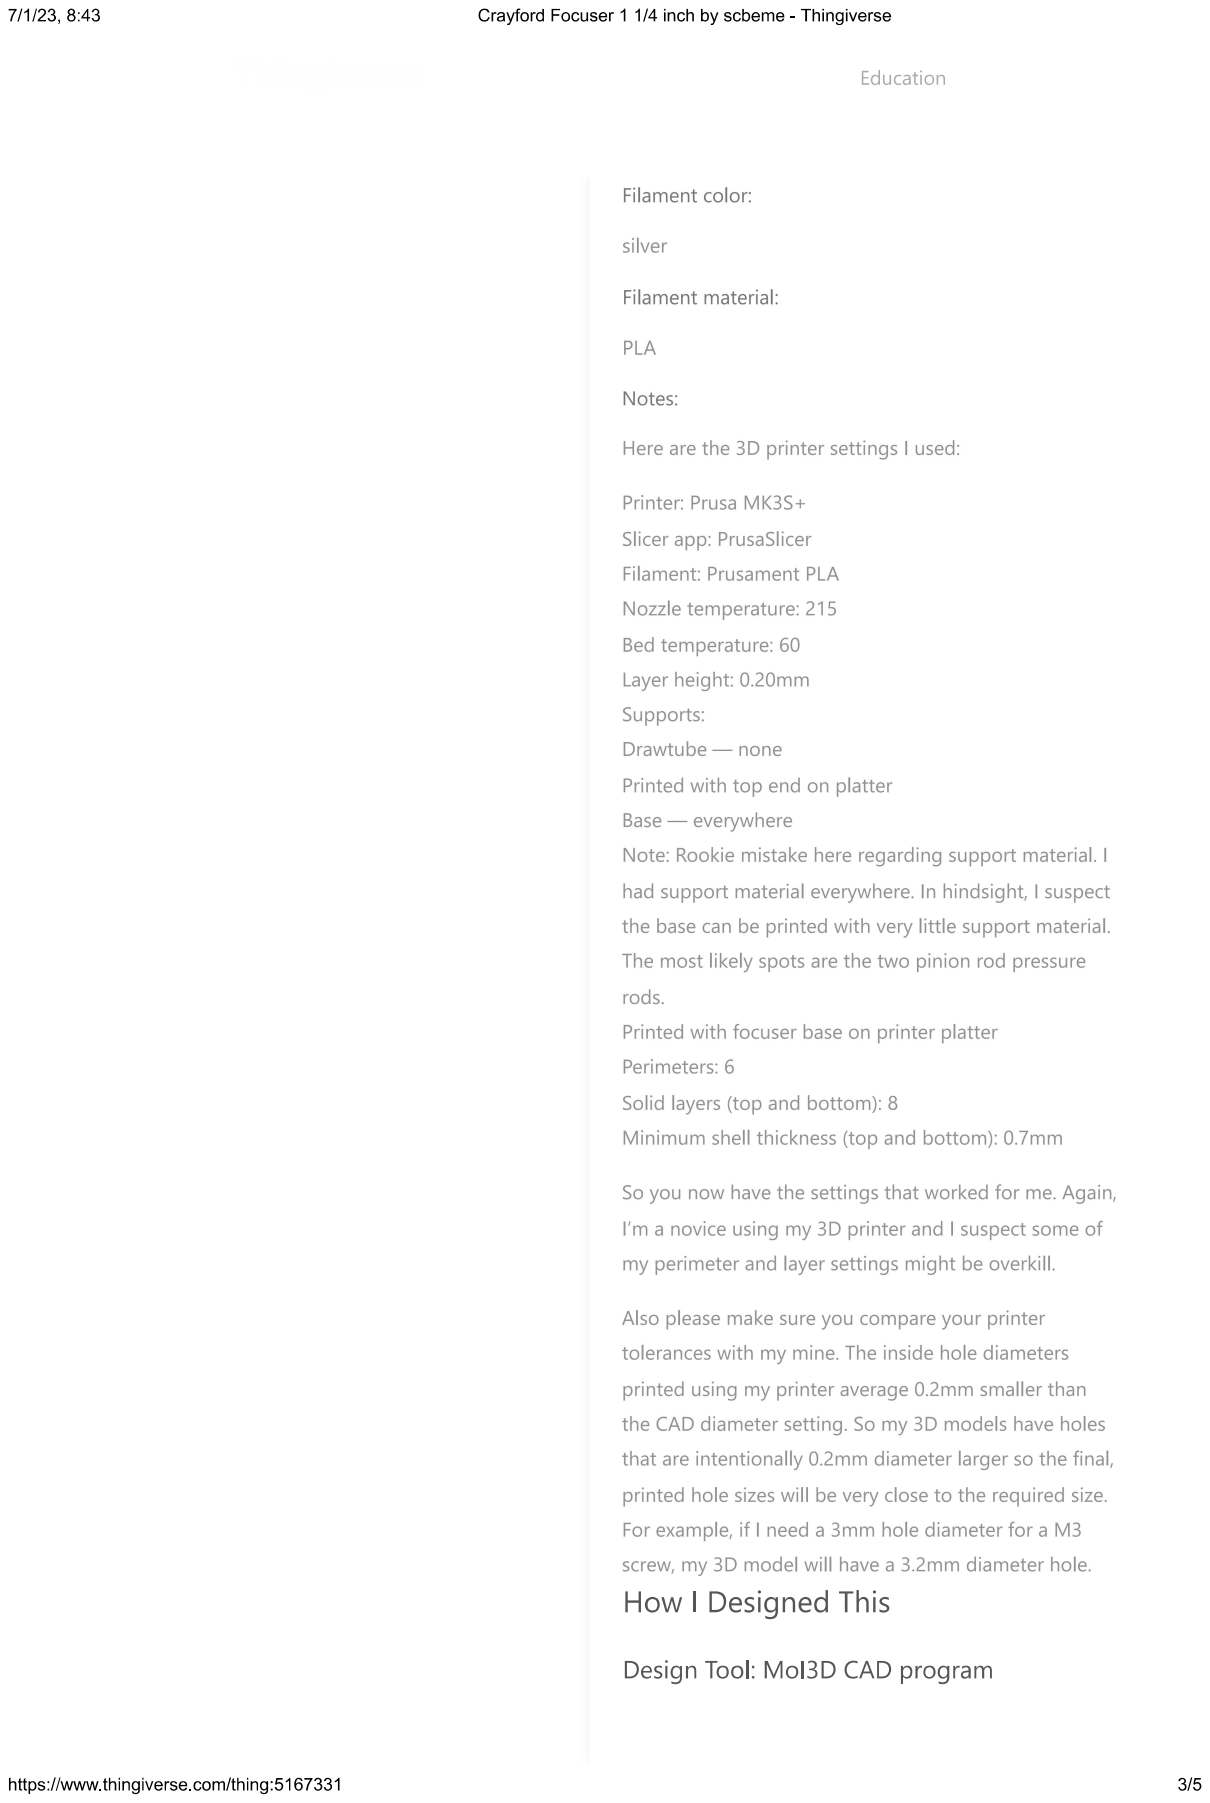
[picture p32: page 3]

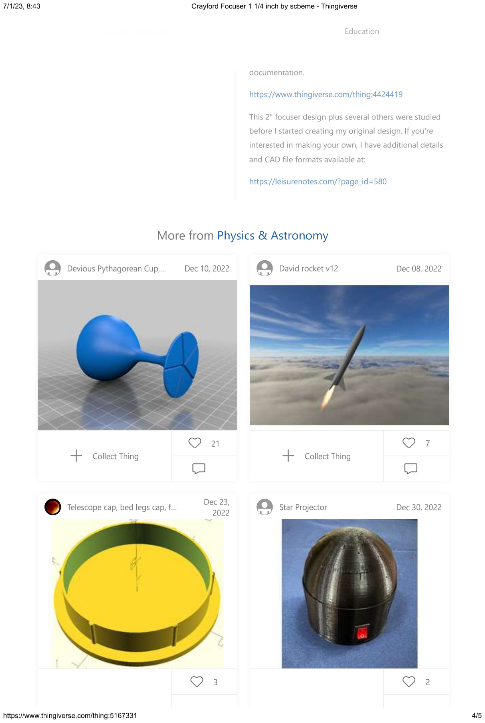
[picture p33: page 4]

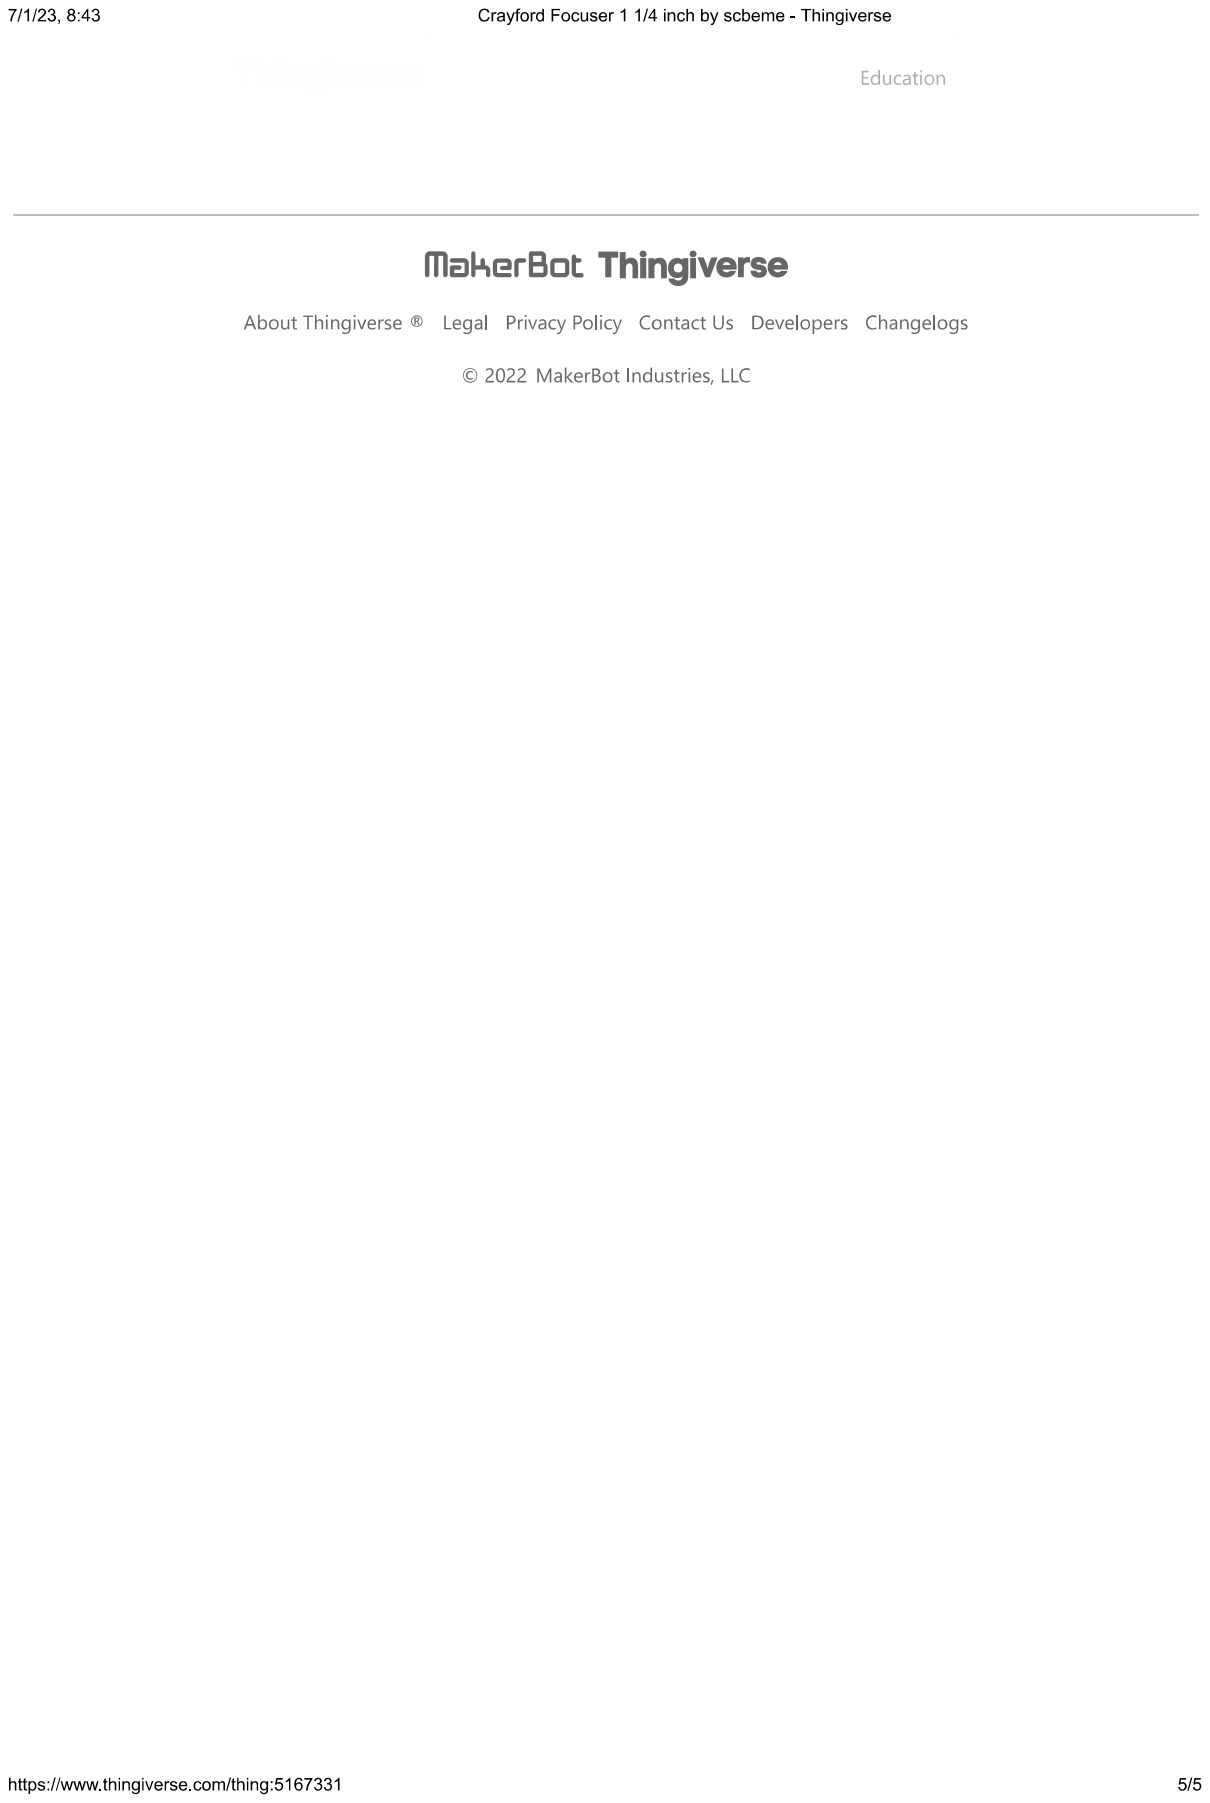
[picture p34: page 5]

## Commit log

2022-09-27 Add files via upload
    changes on primary mirror cell / tab. ready for first printing test
    [humboldt-1.FCStd]
2022-09-28 Add files via upload
    -first printing test
    -finderscope support adapted to vixen polaris
    [humboldt-1-backplate.stl, humboldt-1-finderscope.stl, humboldt-1-primary.cell.stl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]
2022-09-30 Add files via upload
    some UTA work
    [humboldt-1.FCStd]
2023-01-07 inc 3rd party components
    inc. Leavitt lite and crayford focuser
    [focuser_1-25_back.stl, focuser_1-25_base.stl, focuser_1-25_curved_base_10-25_dia.stl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]
2023-01-07 main model update
    [humboldt-2.FCStd]
2023-01-15 Update README.md
    initial BOM
2023-01-15 changing shaft diam from 5 to 4mm)
    closes #3
    [focuser-knob_ver2.stl, focuser-pressure_cylinder_ver2.stl, focuser.FCStd]
2023-01-15 rails to 2mm
    [focuser.FCStd]
2023-01-18 leavitt v2 (jan/17)
    [metric_conversion-Leavitt_Secondary_cell_62.5mm_0.25mm_tol.stl, metric_conversion-Leavitt_Spider_Thick.stl, metric_conversion-Leavitt_UTA_Braced_Focuser_Segmen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]
